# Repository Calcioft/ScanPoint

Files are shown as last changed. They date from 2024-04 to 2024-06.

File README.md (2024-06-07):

# ScanPoint

## Equipe

| Engenharia | Cargo | Membro | Matrícula |
| :- | :- | :- | :--: |
| Software | **Coordenadora geral** | Carla Rocha | 170085023 |
| Software | **Diretora de qualidade** | Brenda Santos | 180041444 |
| Software | **Diretor técnico de Software** | Denniel William | 170161871 |
| Aeroespacial | **Diretora técnica de Estrutura** | Maria Claudia | 200041193 |
| Energia | **Diretora técnica de Eletrônica/Energia** | Carolina Oliveira | 190011483 | 
| Aeroespacial | Desenvolvedor | Cássio Filho | 190011521 |
| Automotiva | Desenvolvedor | Diogo Soares | 190012188 |
| Eletrônica | Desenvolvedor | Miguel Munoz | 221008795 |
| Energia | Desenvolvedor | Lucas Pantoja | 190060352 |
| Software | Desenvolvedora | Ana Carolina | 190101792 |
| Software | Desenvolvedor | Guilherme Basilio | 160007615 |
| Software | Desenvolvedor | Artur de Souza | 190010606 |
| Software | Desenvolvedor | Ciro Costa | 190011611 |
| Software | Desenvolvedor | Vinicius Vieira | 190118059 |
| Software | Desenvolvedor | Pedro Menezes | 190139323 |

## Site

https://lappis-unb.gitlab.io/fga-pi2/semestre-2024-1/grupo-08/scanpoint/

## Como rodar os documentos
[Como rodar os documentos](./how-to-docs.md)

## Reuniões

| Dia | Horário |
| :--: | :--: |
| Quarta-feira | 16:00 - 18:00 |
| Sexta-feira | 14:00 - 18:00 |

## Entregas

### C1

Engloba as fases 1, 2 e 3 do ciclo de vida do projeto, sendo elas: **Problematização**, **concepção e detalhamento da solução** e **projeto e construção de subsistemas da solução proposta**.

**Geral**
- [Arquitetura](docs/geral/anexo.md)
- [Cronograma](docs/geral/cronograma.md)
- [EAP](docs/geral/eap_geral.md)
- [Estimativa de Custos](docs/geral/estimativa-custos.md)
- [Levantamento de riscos](docs/geral/FMEA.md)
- [Requisitos Gerais](docs/geral/requisitos.md)
- [Termo de Abertura](docs/geral/termo_de_abertura_de_projeto.md)
- [Visao geral](docs/geral/visaogeral.md)
- [Integracao de Áreas](docs/geral/integracao.md)

**Software**
- [Arquitetura de software](docs/software/arquitetura.md)
- [Backlog do produto](docs/software/backlog_produto.md)
- [Casos de uso](docs/software/casos-de-uso.md)
- [Diagrama BPMN](docs/software/diagrama-bpmn.md)
- [Diagrama de pacotes](docs/software/diagrama-de-pacotes.md)
- [EAP](docs/software/eap_software.md)
- [Funcionalidades](docs/software/funcionalidades.md)
- [Documento de identidade](docs/software/identidade.md)
- [Prototipo de alta Fidelidade](docs/software/prototipo.md)
- [Requisitos de software](docs/software/requisitos.md)
- [Projeto de subsistema de Software](docs/software/subsistema-software.md)

**Eletrônica/Energia**
- [Arquitetura de Eletrônica](docs/eletronica-energia/arquitetura_eletronica.md)
- [Arquitetura de Energia](docs/eletronica-energia/arquitetura_energia.md)
- [EAP](docs/eletronica-energia/eap.md)
- [Subsistema de Eletrônica](docs/eletronica-energia/Projeto_subsistema_eletronica.md)
- [Subsistema de Energia](docs/eletronica-energia/Projeto_Subsistema_Energia.md)
- [Requisitos](docs/eletronica-energia/requisitos-eletronica-energia.md)

**Estruturas**
- [EAP](docs/estruturas/EAP_estruturas.md)
- [Requisitos](docs/estruturas/Requisitos_estruturas.md)
- [Arquitetura](docs/estruturas/arquitetura_subs_estruturas.md)
- [Subsistema](docs/estruturas/Projeto_subsistema_estruturas.md)
- [Desenhos técnicos](docs/estruturas/DTs.md)
- [Manual de montagem](docs/estruturas/Manual_montagem_estruturas.md)

### C2

Diz respeito à primeira parte da fase 4, a **integração de subsistemas**. Serão feitas:

- Apresentação das adequações realizadas no projeto;
- Demonstração de funcionamento de todos os subsistemas que compõe a solução, já considerando a integração entre as respectivas partes

### C3

Diz respeito à segunda parte da fase 4, a **finalização do produto**. Serão entregues:

- Testes de integração e funcionamento do protótipo de produto;

- Demonstração do funcionamento completo da solução;

- Documentação técnica atualizada nos repositórios do projeto;

- Bannner de apresentação do projeto;

- Vídeo de propaganda da solução, contemplando seu funcionamento completo.

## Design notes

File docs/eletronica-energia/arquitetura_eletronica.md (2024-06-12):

# Arquitetura do Subsistema de Eletrônica

<p style="text-align:justify;">
O principal objetivo da execução do projeto do subsistema eletrônico é de garantir o controle preciso e eficiente do sistema, permitindo o funcionamento adequado do scanner e da mesa rotatória. Para isso, é necessário selecionar e integrar os componentes eletrônicos de forma a atender aos requisitos funcionais e não funcionais estabelecidos.
</p>

<p style="text-align:justify;">
A arquitetura do subsistema envolve motores de passo, microcontroladores Arduino Uno, a ponte H (L298N) e um regulador de tensão LM2596. Os motores de passo controlam a rotação da mesa e a altura da câmera, enquanto os microcontroladores Arduino Uno manipulam os dados de escaneamento e controlam os motores. A ponte H facilita a comunicação entre os motores e os Arduinos, permitindo o controle bidirecional necessário.
</p>

<p style="text-align:justify;">
A alimentação do sistema é fornecida por uma bateria de 12V, com o regulador de tensão LM2596 ajustando a tensão para 5V, conforme necessário para os componentes eletrônicos. Essa configuração assegura que todos os elementos do sistema recebam a energia adequada para um funcionamento estável e eficiente.
</p>

<p style="text-align:justify;">
Ao longo do desenvolvimento, serão realizadas simulações dos circuitos utilizando softwares como Proteus e Fritzing. Essas simulações, juntamente com diagramas de blocos do circuito e diagramas de barramento, proporcionarão uma visão abrangente e detalhada da arquitetura do subsistema eletrônico, facilitando a compreensão e verificação do projeto. 
</p>

## Versionamento

| Versão | Data | Modificação | Autor |
| --- | --- | --- | --- |
| 0.1 | 03/05/2024 | Criação do documento | Carolina Oliveira, Miguel Munoz |
| 0.2 | 03/05/2024 | Adição de versionamento | Ciro Costa  |
| 0.3 | 04/05/2024 | Ajustes de formatação | Ana Carolina |
| 0.4 | 04/05/2024 | Atualização da formatação | Carolina |
| 1.0 | 07/06/2024 | Adequação da Arquitetura conforme feedback do PC 1 | Carolina |

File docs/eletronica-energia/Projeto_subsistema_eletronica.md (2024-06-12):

# Projeto do Subsistema de Eletrônica

<p style="text-align:justify;">
O subsistema eletrônico desempenha o papel de controle sobre os motores, comunicação com o software, integração dos sensores. Nesse contexto, o foco da equipe consistiu na seleção dos componentes eletrônicos e na implementação de estratégias de gerenciamento em conformidade estrita com as normas de segurança elétrica pertinentes.
</p>

## 1. Motor de Passo

<p style="text-align:justify;">
O Motor de Passo é um motor elétrico utilizado para controle de movimentos de forma precisa, este controle é feito através de passos ou graus, com isso é possível controlar o motor sem o uso de sensores para determinar posição. Os motores desse tipo são controlados através de sinais digitais enviados para as suas bobinas, possibilitando a rotação fracionada do eixo, sem a necessidade de escovas internas <a href="#ref-1"> [1]</a>.
</p>

### 1.1. Estrutura do Motor de Passo
<p style="text-align:justify;">
As características do Motor de Passo, no que diz respeito à velocidade, torque e resolução são definidas primeiramente pela estrutura do motor, então é importante conhecer os aspectos internos e a função das peças que compõem o motor.
</p>

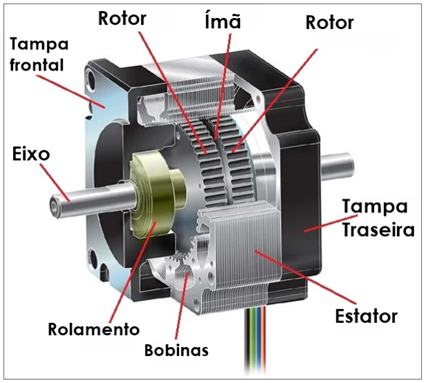
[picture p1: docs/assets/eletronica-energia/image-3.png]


<font size="2"><p style="text-align: center">Figura 1: Estrutura interna do motor de passo <a href="#ref-1"> [1]. </a></p></font>

#### 1.1.1. Rotor
<p style="text-align:justify;">
Uma das partes mais importantes do motor de passo é o rotor, na Figura 1, é mostrado  um motor com rotor híbrido, o corpo que representa o rotor híbrido é composto pelos dois rotores e o imã entre eles, utilizado para a polarização do rotor frontal e o traseiro <a href="#ref-1"> [1]</a>.
</p>

<p style="text-align:justify;">
Existem três configurações possíveis de montagem para o rotor: rotor de imã permanente, rotor de relutância variável e rotor híbrido, o tipo híbrido é o mais comumente utilizado, estas diferenças são apresentadas na Tabela 1.
</p>

<font size="2"><p style="text-align: center">Tabela 1: Diferenças entre os rotores.</p></font>

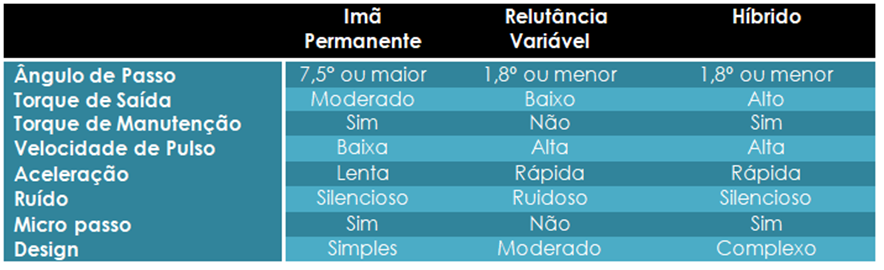
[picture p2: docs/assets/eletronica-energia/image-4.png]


#### 1.1.2. Estator
<p style="text-align:justify;">
O Estator produz o campo magnético que causa a movimentação do rotor. Para análise do estator é necessário tomar nota de alguns pontos como: o número de fases, de par de polos e configuração do fio. A fase ou o par de polos é formado por duplas de bobinas que são energizadas simultaneamente.
</p>

<p style="text-align:justify;">
A estrutura do estator é formada por polos magnéticos dentados, sendo que cada polo é dotado de uma bobina com o seu par oposto, de forma que os pares são energizados simultaneamente e por consequência são magnetizados com a mesma polaridade, os dois polos formam uma fase. 
</p>

<p style="text-align:justify;">
O primeiro modelo do exemplo abaixo é do tipo estator bifásico, com fases A e B, enquanto o segundo é do tipo estator trifásico, com fases A, B e C.
</p>

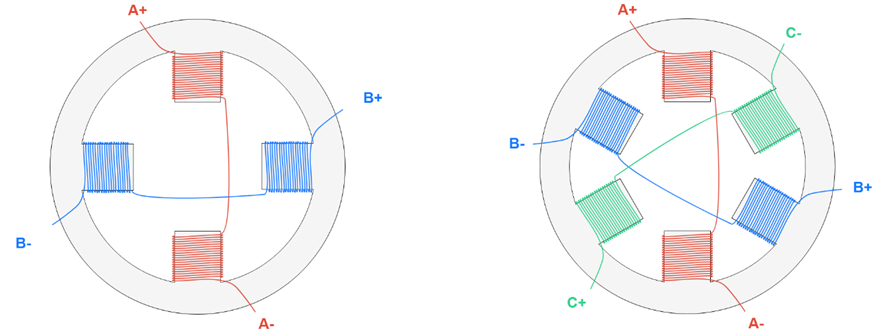
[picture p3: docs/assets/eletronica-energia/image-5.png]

<font size="2"><p style="text-align: center">Figura 2: Modelo de um estator bifásico.</p></font>

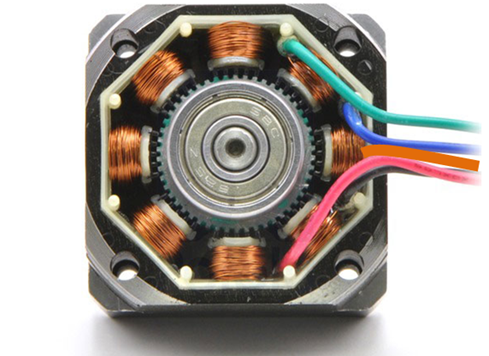
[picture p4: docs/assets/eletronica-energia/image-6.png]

<font size="2"><p style="text-align: center">Figura 3: Estator real.</p></font>

<p style="text-align:justify;">
A Figura 2, mostra uma representação gráfica da distribuição das bobinas no estator, já a Figura 3, mostra uma imagem de um estator real, com seus dentes e bobinas em enrolamento de cobre.
</p>

<p style="text-align:justify;">
O eixo do motor híbrido é construído com dois grupos dentados de rotores, um deles polarizados com polo sul e outro com polo norte.
</p>

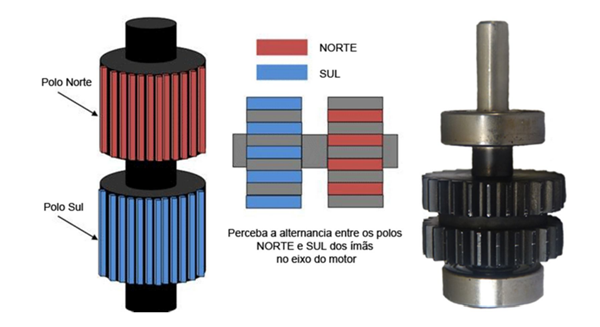
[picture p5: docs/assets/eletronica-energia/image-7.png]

<font size="2"><p style="text-align: center">Figura 4: Modelo do eixo do motor <a href="#ref-1"> [1]</a>.</p></font>

### 1.2. Tipos de Polos
<p style="text-align:justify;">
Existem dois modelos de acordo com os polos, o bipolar e o unipolar, os termos surgiram de conformidade com os drivers que são utilizados para acionamento desses motores. O polar do termo representa "polaridade” e se refere ao driver utilizado para controle desses motores, utilizaremos as expressões "motor unipolar” e "motor bipolar” por convenção social <a href="#ref-1"> [1]</a>.
</p>
 
#### 1.2.1. Unipolar
<p style="text-align:justify;">
O modelo utilizado com o driver Unipolar conta com duas bobinas por fase, formando um par de polos, além disso, há o contato em comum, dessa forma os motores desse tipo podem ter 5, 6 ou 8 fios <a href="#ref-1"> [1]</a>.
</p>

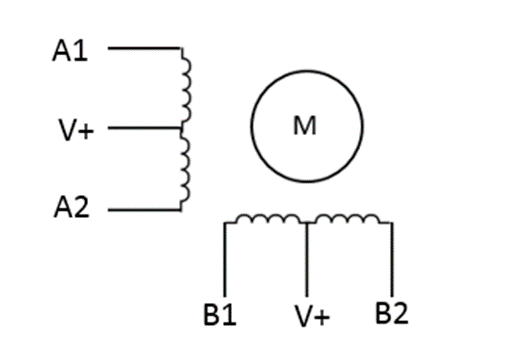
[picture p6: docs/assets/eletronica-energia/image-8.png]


<font size="2"><p style="text-align: center">Figura 5: Driver unipolar <a href="#ref-1"> [1]</a>.</p></font>

<p style="text-align:justify;">
Com o fio central é possível controlar a direção da corrente, no entanto apenas metade da bobina pode ser utilizada, isso faz com que o motor seja menos eficiente se comparado ao bipolar. O fio central é conectado ao Vin do circuito, sendo que se o Mosfet 1 estiver ativo, a corrente fluirá de Am para A+, se o Mosfet ativo for o 2, a corrente fluirá de Am para A-.
</p>

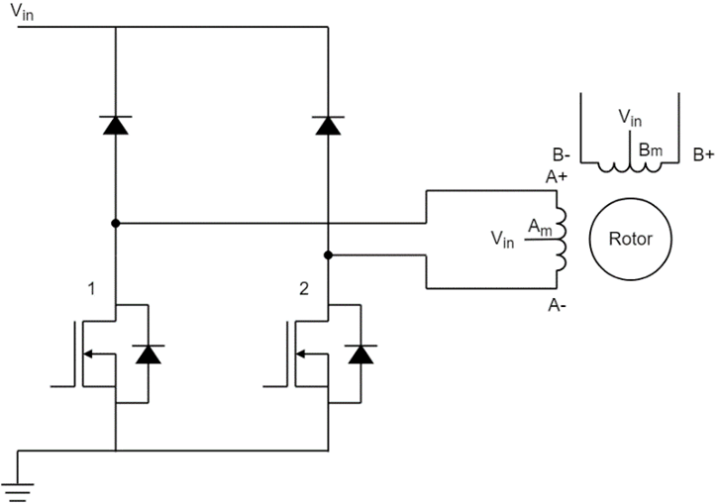
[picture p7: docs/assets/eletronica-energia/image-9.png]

<font size="2"><p style="text-align: center">Figura 6: Diagrama circuito unipolar <a href="#ref-1"> [1] </a>.</p></font>

#### 1.2.2. Bipolar
<p style="text-align:justify;">
No motor do tipo bipolar, cada bobina é composta por dois fios apenas, sem derivações centrais como as do tipo unipolar, de forma que são motores mais fáceis de serem produzidos.
</p>

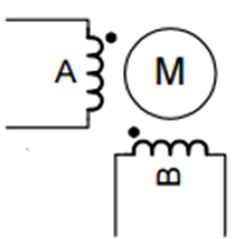
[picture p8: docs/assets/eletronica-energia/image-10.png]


<font size="2"><p style="text-align: center">Figura 7: Driver bipolar <a href="#ref-1"> [1]</a>.</p></font>

<p style="text-align:justify;">
Como não há a derivação central, para controle de direção é necessário utilizar uma ponte H, exigindo um circuito de acionamento mais complexo. Para os motores desse tipo, temos que a corrente flui de A- para A+ quando os Mofets 2 e 3 estão ativos, e flui de A+ para A- quando 1 e 4 estão ativos. Apesar de possuir um acionamento mais complexo, os motores do tipo bipolar são mais comuns, pois permitem que o motor atinja maior torque <a href="#ref-1"> [1]</a>. Importante mencionar que, para o desenvolvimento deste projeto, os motores bipolares foram adotados pois, além da disponibilidade desses componentes no laboratório da UnB, eles exigem a manipulação de menos fios, economizando conexões nas placas de controle que serão compartilhadas.
</p>

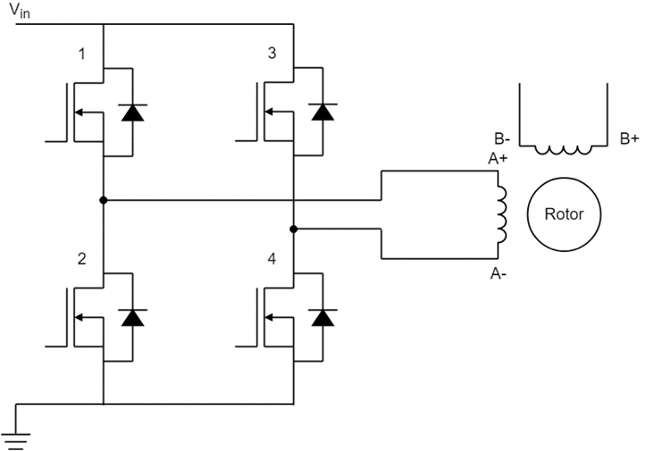
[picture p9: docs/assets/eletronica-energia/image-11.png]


<font size="2"><p style="text-align: center">Figura 8: Diagrama circuito bipolar <a href="#ref-1"> [1]</a>.</p></font>

### 1.3. Funcionamento de um motor de passo
<p style="text-align:justify;">
O motor de passo é um dispositivo eletromecânico composto por bobinas (indutores) e um rotor magnético (ímã permanente ou imantado). As bobinas convertem energia elétrica em campo magnético, alinhando o rotor a esse campo. A excitação correta das bobinas faz o rotor, que gira em torno de seu eixo, mover-se no sentido desejado, convertendo energia magnética em movimento (energia mecânica). O rotor é rotacionado em pequenos incrementos angulares, chamados de "passos" <a href="#ref-2"> [2]</a>.

O funcionamento básico do motor de passo envolve o uso de bobinas alinhadas dois a dois. Quando energizadas, elas atraem o rotor, alinhando-o com o campo magnético gerado, resultando em uma variação angular pequena, chamada de passo. A velocidade e o sentido de movimento são determinados pela forma como cada bobina é ativada, incluindo a ordem e a velocidade entre cada processo de ativação <a href="#ref-2"> [2]</a>.

As vantagens do motor de passo incluem sua precisão de posicionamento e torque aplicado, além de ter uma resposta excelente na aceleração e desaceleração, devido à sua lógica digital. No entanto, ele pode apresentar baixo desempenho em alta velocidade, requer um certo grau de complexidade para operação e pode sofrer ressonância devido a um controle inadequado <a href="#ref-2"> [2]</a>.

Complementando com o banco de dados, o motor de passo é frequentemente utilizado em aplicações que exigem precisão de posicionamento, como impressoras 3D, máquinas CNC e robótica industrial. Ele oferece um controle preciso sobre o movimento, o que é essencial em muitas aplicações. Além disso, o motor de passo pode ser facilmente controlado por microcontroladores, o que o torna uma escolha popular em projetos eletrônicos e de automação <a href="#ref-2"> [2]</a>.

A figura a seguir mostra como um motor de passo pode ser controlado mediante lógica binária:
</p>
 
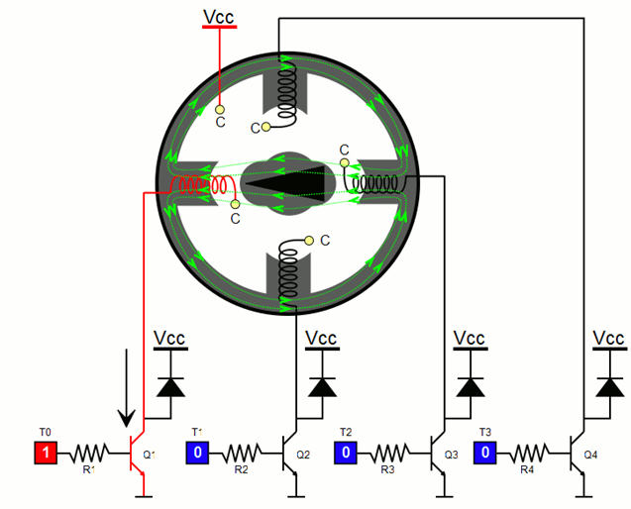
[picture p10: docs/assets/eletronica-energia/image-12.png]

<font size="2"><p style="text-align: center">Figura 9: Motor de passo controlado pelas entradas To até T3 <a href="#ref-2"> [2]</a>.</p></font>

## 2. Placa Arduino Uno
<p style="text-align:justify;">
O Arduino Uno é uma placa microcontrolada baseada no chip ATmega328. Esta placa é muito utilizada no desenvolvimento de projetos embarcados, é hoje em dia é a mais utilizada e documentada da família Arduino.
</p>

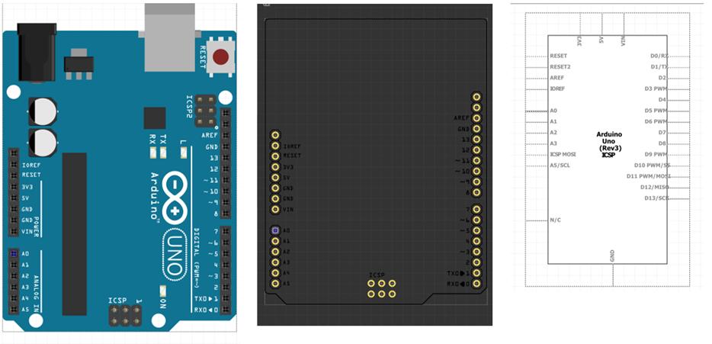
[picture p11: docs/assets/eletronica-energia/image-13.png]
   

<font size="2"><p style="text-align: center">Figura 10: Placa Arduino Uno, diagrama de barramento e diagrama esquemático. Fonte: Autoria própria.</p></font>

<p style="text-align:justify;">
A placa conta com um chip ATmega328 que é um microcontrolador único desenvolvido pela Atmel, pertencente à família megaAVR. A arquitetura do Arduino Uno segue o padrão Harvard e possui um núcleo de processador RISC de 8 bits customizado.
</p>

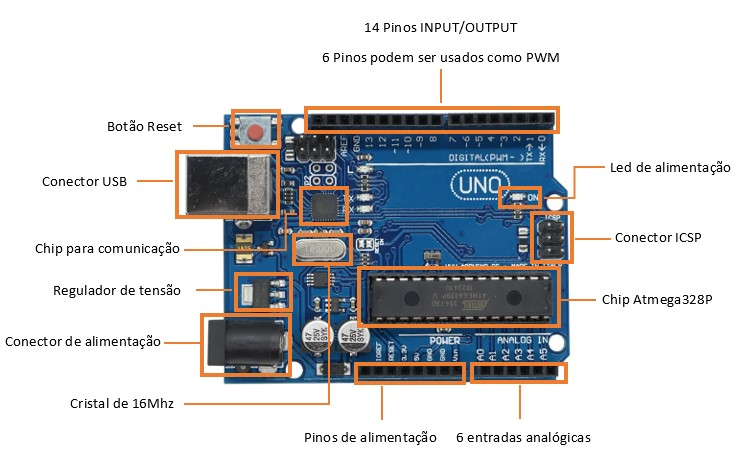
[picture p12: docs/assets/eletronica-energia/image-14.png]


<font size="2"><p style="text-align: center">Figura 11: Diagrama de pinos da placa Arduino Uno <a href="#ref-3"> [3]</a>.</p></font>

### 2.1. Características principais do Arduino Uno

 - A tensão de operação é 5V
 - A tensão de entrada recomendada varia de 7V a 12V
 - A tensão de entrada varia de 6V a 20V
 - 14 pinos de entrada/saída digital
 - 6 pinos analógicos
 - A corrente DC para cada pino de entrada/saída é de 40 mA
 - A corrente DC para o pino de 3,3 V é 50 mA
 - A memória flash é de 32 KB
 - SRAM é 2KB
 - EEPROM é 1 KB
 - A velocidade do CLK é de 16 MHz

### 2.2. Diagrama de pinos do Arduino Uno
<p style="text-align:justify;">
A placa do Arduino Uno conta com uma grande variedade de pinos de alimentação, pinos analógicos, ATmega328, conector ICSP, botão Reset, LED de alimentação, pinos digitais, led de teste, pinos TX/RX, interface USB e fonte de alimentação externa, na Figura 12, se apresentam estes pinos.
</p>

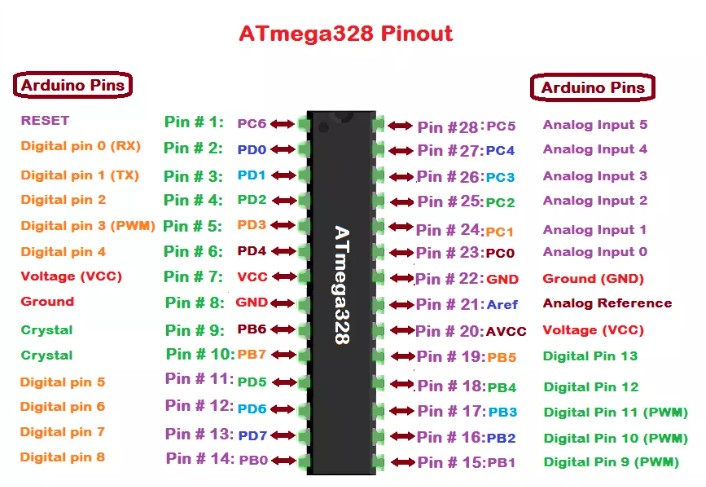
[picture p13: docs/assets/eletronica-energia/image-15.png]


<font size="2"><p style="text-align: center">Figura 12: Diagrama de Pinos do microcontrolador ATmega328.</p></font>

<p style="text-align:justify;">
A seguir se faz a descrição de cada um dos componentes do diagrama na Figura 12.
</p>

#### 2.2.1. Descrições principais para utilização do Arduino Uno

##### 2.2.1.1. Fonte de Alimentação
<p style="text-align:justify;">
Esta placa conta com uma grande vantagem e é poder ligar ela de forma externa com ajuda de um cabo USB ou uma fonte de alimentação externa, além disso, as fontes de alimentação externas incluem principalmente um conversor AC para DC, caso contrário, uma bateria. A fonte deve ser inserida no conector de alimentação da placa Arduino. Suas faxas de tensão estão entre 7 e 12 Volts,  conta com um pino GND e conector POWER <a href="#ref-3"> [3]</a>.
</p>

##### 2.2.1.2. Entradas e saídas digitais
<p style="text-align:justify;">
O Arduino Uno possui 14 pinos que podem ser usados como entrada ou saída a depender da necessidade do programador. Com a ajuda de funções como pinMode(), digitalWrite() e Digital Read() é possível definir como os pinos serão utilizados <a href="#ref-3"> [3]</a>.
</p>

##### 2.2.1.3. Entradas analógicas
<p style="text-align:justify;">
A placa Arduino UNO conta com 6 canais de conversor analógico para digital, nomeadas de A0 a A5. Sendo que a resolução do conversor analógico digital é de 10Bits. Isso significa que este irá mapear tensões entre 0 e a tensão operacional (5V ou 3.3V) para valores inteiros entre 0 e 1023. No Arduino UNO, isso permite uma resolução entre leituras de: 5 volts / 1024 unidades, ou .0049 volts (4.9 mV) por unidade. Essas entradas são nomeadas de A0 a A5. A função analogRead() lê o valor de um pino analógico especificado <a href="#ref-3"> [3]</a>.
</p>

#### 2.2.2. Pino (TX) e Pino (RX) (Serial):

<p style="text-align:justify;">
  Os pinos 0 e 1 são usados para transmitir e receber dados seriais TTL, e estes são conectados aos pinos equivalentes do chip ATmega8U2 USB para TTL Serial <a href="#ref-3"> [3]</a>.
</p>

#### 2.2.3. Pinos externos de interrupção:
<p style="text-align:justify;">
Os pinos 2 e 3 do Arduino Uno podem desempenhar a função de entrada de sinal para interrupção externa tais funções são nomeadas de INT0 e INT1, respectivamente <a href="#ref-3"> [3]</a>.
</p>

#### 2.2.4. Pinos 3, 5, 6, 9, 10 e 11 (PWM):
<p style="text-align:justify;">
O Arduino Uno possui 6 pinos para saída PWM, são estes os pinos 3, 5, 6, 9, 10 e 11. Para auxiliar na manipulação desses pinos a plataforma possui uma função que auxilia na escrita de valores chamada de "duty cycle” facilitando a utilização do PWM do Arduino Uno, o qual pode ser acoplado com módulos externos <a href="#ref-3"> [3]</a>.
</p>

#### 2.2.5. Pinos SPI (Pino-10 (SS), Pino-11 (MOSI), Pino-12 (MISO), Pino-13 (SCK):
<p style="text-align:justify;">
SPI (Serial Peripheral Interface) é um protocolo de comunicação serial, a SPI possui uma conexão full duplex, o que significa que os dados são enviados e recebidos simultaneamente. O SPI pode ser utilizado para a comunicação entre dois arduinos <a href="#ref-3"> [3]</a>.
</p>

#### 2.2.6. LED Interno Pino 13
<p style="text-align:justify;">
A placa do Arduino Uno possui um Led interno conectado ao pino 13 (pino digital). Como pino de valor ALTO, o diodo emissor de luz é ativado, sempre que o pino estiver em nível BAIXO <a href="#ref-3"> [3]</a>.
</p>

#### 2.2.7. Pino-4 (SDA) e Pino-5 (SCL) (I2C):
<p style="text-align:justify;">
Permite comunicação TWI (Two Wire Interface) com a ajuda da biblioteca Wire <a href="#ref-3"> [3]</a>.
</p>

#### 2.2.8. AREF (Tensão de Referência):
<p style="text-align:justify;">
AREF significa Referência Analógica. Ele permite alimentar o Arduino com uma tensão de referência de uma fonte de alimentação externa para configurar a tensão de referência usada para entrada analógica (ou seja, o valor usado como o topo da faixa de entrada) <a href="#ref-3"> [3]</a>.
</p>

#### 2.2.9. Pino de Reset:
<p style="text-align:justify;">
Este pino é usado para resetar (RST) o microcontrolador <a href="#ref-3"> [3]</a>.
</p>
 
### 2.3. Memória
<p style="text-align:justify;">
A memória do microcontrolador Atmega328 do Arduino Uno inclui memória flash de 32 KB para armazenamento de código, SRAM-2 KB e EEPROM-1 KB <a href="#ref-3"> [3]</a>.
</p>

### 2.4. Comunicação
<p style="text-align:justify;">
O Arduino Uno ATmega328 oferece comunicação serial UART TTL e é acessível em pinos digitais como TX (1) e RX (0). O software de um Arduino possui um monitor serial que permite dados fáceis. Existem dois LEDs na placa, como RX e TX, que piscarão sempre que os dados estiverem sendo transmitidos através do USB.
</p>

<p style="text-align:justify;">
A biblioteca SoftwareSerial permite a comunicação serial nos pinos digitais do Arduino Uno e o ATmega328P suporta TWI (I2C), bem como comunicação SPI. O software Arduino contém uma biblioteca cabeada para simplificar a utilização do barramento I2C <a href="#ref-3"> [3]</a>.
</p>

### 2.5. Proteção de alta tensão do USB
<p style="text-align:justify;">
A placa Arduino Uno possui um fusível que protege a porta USB do PC de sobretensão. Embora a maioria dos PCs tenha sua própria proteção interna, o fusível oferece uma proteção adicional de segurança <a href="#ref-3"> [3]</a>.
</p>

### 2.6. Características físicas
<p style="text-align:justify;">
As características físicas de uma placa Arduino incluem principalmente comprimento e largura. O comprimento e a largura da placa de circuito impresso do Arduino Uno são 2,7 X 2,1 polegadas, mas o conector de alimentação e o conector USB se estenderão além dessa medida. A placa pode ser fixada na superfície, caso contrário, com os orifícios dos parafusos <a href="#ref-3"> [3]</a>.
</p>

## 3. Modulação PWM
<p style="text-align:justify;">
A modulação por largura de pulso (PWM) é uma técnica fundamental que envolve a variação da largura dos pulsos em um sinal elétrico para transmitir informações. Em vez de manter um sinal em níveis constantes, o PWM altera a largura dos pulsos, controlando o tempo em que a chave fica ligada e desligada. Isso permite administrar a quantidade média de energia que chega à carga e, consequentemente, a potência elétrica <a href="#ref-4"> [4]</a>.

Essa técnica é amplamente utilizada em diversos equipamentos eletrônicos de potência, como drivers de LED, inversores de frequência e controle de velocidade de motores. No cotidiano, o PWM é encontrado em carregadores, sistemas fotovoltaicos, servo-motores e carros elétricos, entre outros <a href="#ref-7"> [7]</a>.

O ciclo de trabalho, ou Duty Cycle mostrado na figura, é um parâmetro crucial para controlar um sinal PWM. Ele representa a relação entre a largura do pulso e o período, informando o tempo em que o sinal está em nível alto (ligado) e o tempo em que está em nível baixo (desligado). 

O Duty Cycle é expresso em porcentagem e calculado pela fórmula D = (PW / T) x 100%, onde PW é a largura do pulso e T é o período <a href="#ref-5"> [5]</a>. Deste modo, o sinal 255 da placa é convertido para um sinal PWM de 100%, e o sinal 0 da placa é convertido para um sinal PWM de 0%. Portanto um sinal de 127 da placa será convertido para um sinal PWM de 50%. Consequentemente, para um motor, o sinal 0 seria o motor parado, já o sinal 255 seria a sua rotação máxima. Abaixo é possível ver um exemplo com o sinal PWM sendo aplicado em um LED <a href="#ref-5"> [5]</a>.
</p>

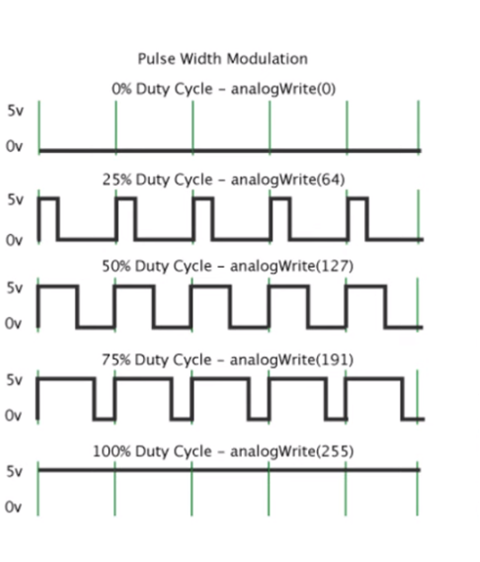
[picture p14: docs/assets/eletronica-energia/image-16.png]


<font size="2"><p style="text-align: center">Figura 13: Representação do comportamento do controle PWM.</p></font>

<p style="text-align:justify;">
Uma das principais vantagens do PWM é a manutenção do sinal digital em todo o percurso, o que minimiza os efeitos de ruído. Além disso, o PWM oferece maior imunidade ao ruído em comparação ao controle analógico, o que torna essa técnica ideal para comunicações. Em sistemas de freios controlados por modulação, por exemplo, o PWM é utilizado para controlar a pressão exercida pelo freio de acordo com a quantidade de tensão ou corrente aplicada <a href="#ref-4"> [4]</a>.
</p>

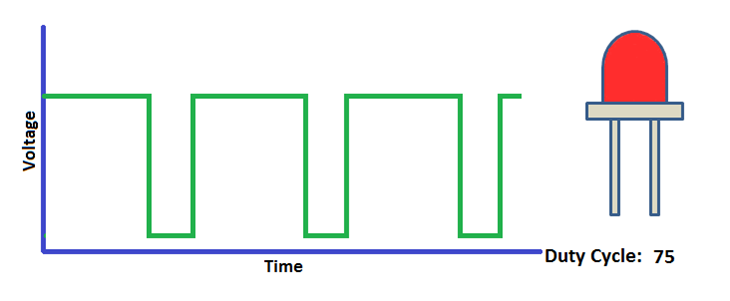
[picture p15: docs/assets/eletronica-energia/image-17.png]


<font size="2"><p style="text-align: center">Figura 14: Funcionamento do PWM num led.
Fonte <a href="#ref-5"> [5]</a>.</p></font>

## 4. Driver Motor de Passo A4988

<p style="text-align:justify;"> O Driver A4988 é um componente eletrônico utilizado para controlar motores de passo bipolares, com capacidade de pequenos passos (microstepping) para maior suavidade e precisão na movimentação dos motores.  A tensão de operação lógica do driver é de 3-5,5V, que são conectados nos pinos VDD e GND. Pode controlar motores de até 35V e 2A por bobina (picos de 4A), além disso, é capaz de controlar o motor com até 1/16 passos <a href="#ref-4"> [9]</a>
</p>

### 4.1. Calibração

<p style="text-align:justify;">
Para calibrar o driver de motor faz-se o ajuste do trimpot integrado à placa. Para realizar a calibração deve-se utilizar a seguinte fórmula para cálculo da tensão de referência:
</p>

Vref = Imotor x 8 x Rsense

<p style="text-align:justify;">
Onde Vref é a tensão de referência que devemos chegar no ajuste do driver, 8 é uma constante arbitrária específica para o A4988, e Rsense é o resistor de detecção de corrente presente no driver e Imotor é a corrente de trabalho no motor.  A corrente máxima de um motor está indicada no seu datasheet, e em geral recomenda-se utilizar até 70% desse valor <a href="#ref-4"> [9]</a>.
</p>

### 4.2. Ajuste do A4988

<p style="text-align:justify;">
Com o valor da tensão de referência determinado, precisamos fazer o ajuste do potenciômetro. Não é preciso que o driver esteja conectado na placa da aplicação final, basta ligar os pinos RST e SLP do driver e alimentar parte lógica através dos pinos Vdd e GND do módulo. Com essas ligações, é medido com um multímetro a tensão entre o GND e a parte metálica do trimpot, onde é feito o ajuste. Girar o potenciômetro no sentido horário aumenta a tensão e no sentido anti-horário diminui. O ajuste deve ser feito até a leitura do multímetro coincidir com a tensão calculada <a href="#ref-4"> [9]</a>. </p>

### 4.3. Uso do driver A4988
<p style="text-align:justify;">
Para usar o driver é simples, conecte a alimentação do motor aos pinos Vmot e GND e a alimentação da parte lógica aos pintos Vdd e GND. O pino DIR controla a direção em que o motor deve girar e o pino STEP faz o motor dar um passo a cada pulso que recebe <a href="#ref-4"> [9]</a>.</p>

### 4.4. Especificações técnicas do Driver Motor de Passo A4988
– Chip: A4988 (datasheet)
– Controle de passos e direção.
– Tensão lógica: 3-5,5V
– Tensão saída motores: 8-35V
– 5 Resoluções: full-step, half-step, 1/4-step, 1/8-step e 1/16-step.
– Regulador de tensão embutido.
– Proteção conta sobrecarga de corrente e curto-circuito.
 
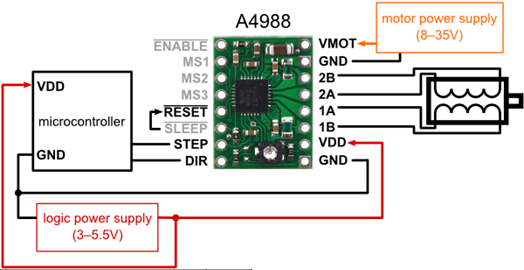
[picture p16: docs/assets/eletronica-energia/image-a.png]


<font size="2"><p style="text-align: center">Figura 15: Diagrama esquemático do drive A4988.
Fonte <a href="#ref-5"> [9]</a>.</p></font>

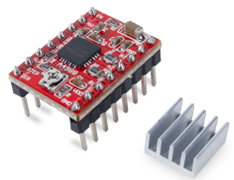
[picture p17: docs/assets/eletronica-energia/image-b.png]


<font size="2"><p style="text-align: center">Figura 16: Drive do motor de passo.
Fonte <a href="#ref-5"> [5]</a>.</p></font>

Tabela: Conexões do driver A4988 <a href="#ref-5"> [6]</a>.</p>

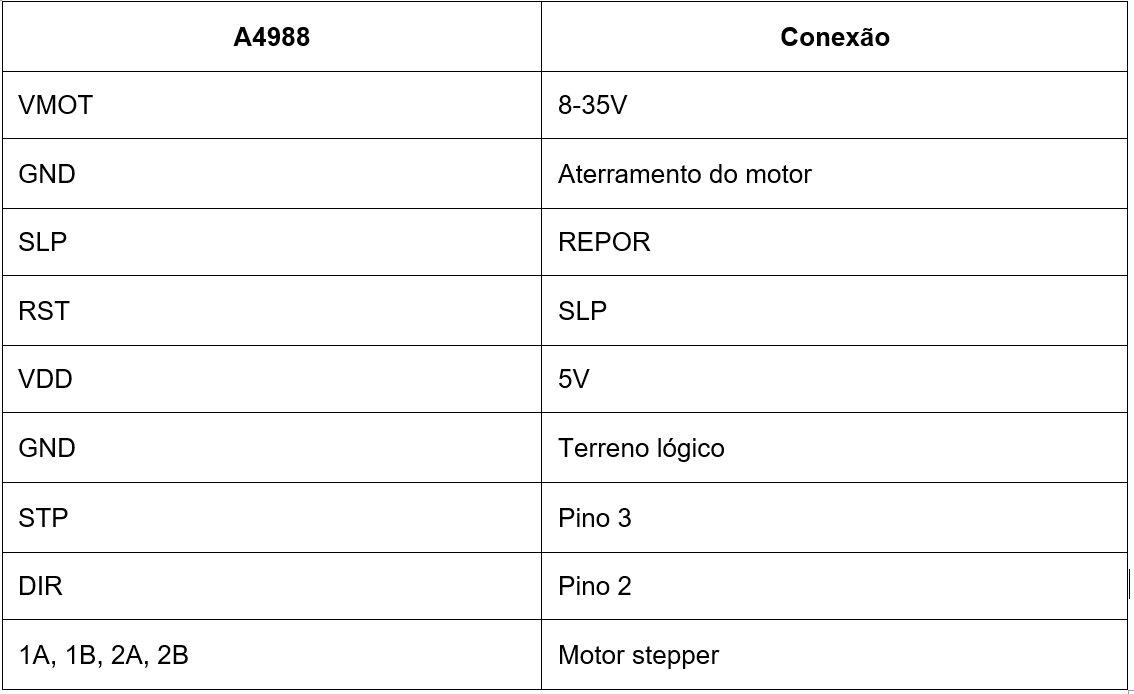
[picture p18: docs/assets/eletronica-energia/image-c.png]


### 4.5. Sensores de Distância Laser VL53L0X
<p style="text-align:justify;">
O VL53L0X é um sensor de distância infravermelho de alta precisão, produzido pela STMicroelectronics, conhecido como o menor sensor do mercado. Utiliza um VCSEL (Laser Emissor de Superfície de Cavidade Vertical) com filtros para evitar interferências de luz externa, aumentando seu alcance. Funciona como um sensor Time of Flight (ToF), emitindo uma luz invisível que reflete em obstáculos, e calcula a distância com base no tempo de retorno dessa luz, alcançando até 2 metros <a href="#ref-4"> [10]</a>.

O módulo VL53L0X, também conhecido como GY-VL53L0XV2, CJVL53L0XV2 ou VL53L0XV2, é compatível com várias placas Arduino. É compacto, preciso, possui regulador de tensão integrado, permitindo alimentação de 3V ou 5V, e vem em várias cores, todas com as mesmas funcionalidades. A comunicação é realizada via interface I2C  <a href="#ref-4"> [10]</a>. </p>

### 4.6. Pinagem
<p style="text-align:justify;">
Além de pinos de alimentação (VIN e GND), o módulo VL53L0X possui dois pinos dedicados a comunicação I2C (SCL e SDA), um pino de reset (XSHUT) e um pino de saída de dados (GPIO1) que pode ser utilizado para programar interrupções no microcontrolador ao qual o sensor está ligado  <a href="#ref-4"> [11]</a>.
</p>

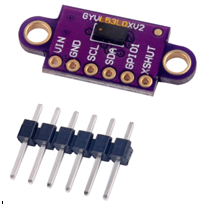
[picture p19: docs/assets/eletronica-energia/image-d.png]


<font size="2"><p style="text-align: center">Figura 17: Módulo VL53L0X.
Fonte <a href="#ref-5"> [11]</a>.</p></font>

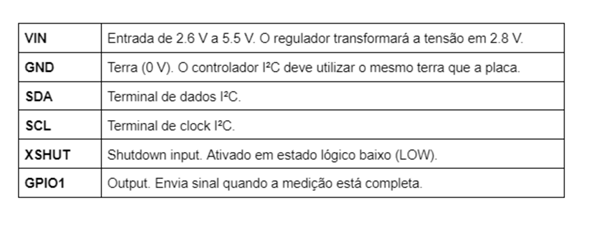
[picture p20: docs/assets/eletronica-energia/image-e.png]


<font size="2"><p style="text-align: center">Figura 18: descrição dos pinos do VL53L0X.
Fonte <a href="#ref-5"> [11]</a>.</p></font>

## 5. Módulo Regulador C/LM2596
<p style="text-align:justify;">
O circuito precisa de um módulo que permita trabalhar com duas tensões, uma de 12V para alimentar a Ponte H, e um de 5V para alimentar a placa de árduino, para resolver esta situação foi trabalhado com um fonte de 12V e um módulo regular C/LM2596 (ver figura 16 e 17). O Módulo Regulador de Tensão LM2596 trabalha como um conversor DC DC no modo Step Down, sendo capaz de reduzir uma carga de até 3A com ótima eficiência. 

A tensão de saída pode ser ajustada entre 1,5 a 35v, tendo como entrada 3,2 a 40v. Possui uma velocidade de comutação de 150KHz e pode ser aplicado em circuitos onde a saída de um sensor é superior a 5v, tensão de entrada máxima em um Arduino ou PIC <a href="#ref-8"> [8]</a>.
</p>

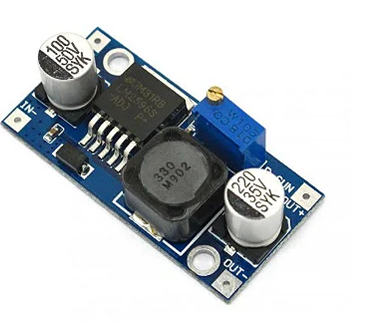
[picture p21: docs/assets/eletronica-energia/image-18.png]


<font size="2"><p style="text-align: center">Figura 19: Módulo regular C/LM2596.</p></font>

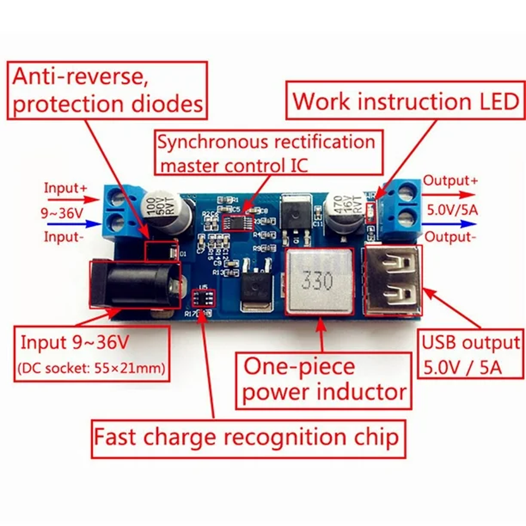
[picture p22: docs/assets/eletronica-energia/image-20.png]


<font size="2"><p style="text-align: center">Figura 20: Especificação dos componentes do módulo regulador C/LM2596.</p></font>

<p style="text-align:justify;">
Este módulo tem as seguintes carácterísticas:
</p>

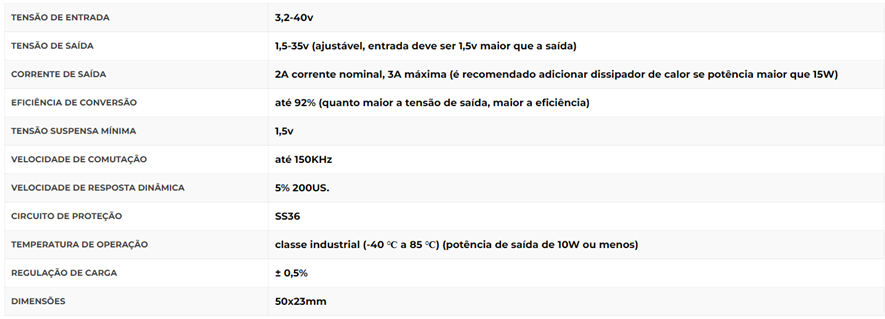
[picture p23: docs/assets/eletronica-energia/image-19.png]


<p style="text-align:justify;">
Assim conhecendo todos os componentes, foi montada uma simulação utilizando programa wokwi, a qual é motrada na Figura 21, esta simulação foi importante para verificar o funcinamento da programação antes de realizar testes reais. Já na Figura 22, encontra-se a representação do circuito realizada utilizando o Fritzing que permite gerar o diagrama esquemáticos e de barramento os quais são apresentados nas figuras 23 e 24 respectivamente </p>

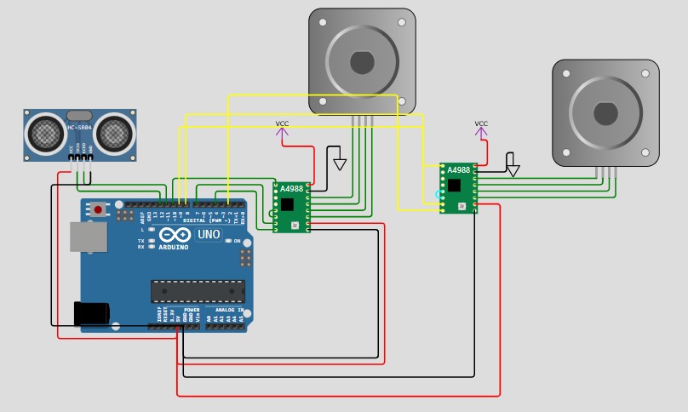
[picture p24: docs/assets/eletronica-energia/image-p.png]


<font size="2"><p style="text-align: center">Figura 21: Simulação do wokwi do sistema de motores.</p></font>



<font size="2"><p style="text-align: center">Figura 22: Sistema realizado no Fritzing para gerar os diagramas.</p></font>



<font size="2"><p style="text-align: center">Figura 23: Diagrama de blocos completo do circuito com motores de passo.</p></font>



<font size="2"><p style="text-align: center">Figura 24: Diagrama de barramentos completo do circuito com motores de passo.</p></font>

## 6. Descrição Matemática do Motor
<p style="text-align:justify;">
Um motor pode ser modelado utilizando um Resistor, um indutor e uma força contra eletromotriz que relaciona o fluxo magnético gerado pelo motor em função do fluxo magnético e do número de espiras que ele tem, sendo assim esta força é modelada pela relação de Faraday como se mostra na equação 1:
</p>



<p style="text-align:justify;">
A equação que representa a tensão pode ser modelada aplicando a LKT, representada como mostra a equação 2 e a Figura 25:
</p>





<font size="2"><p style="text-align: center">Figura 25: Modelo Elétrico do motor DC.</p></font>

<p style="text-align:justify;">
O motor pode ser separado em variáveis elétricas e mecânicas, conforme mostra a figura 26, onde a parte ressaltada na cor preto, indica a parte elétrica e a ressaltada na cor vermelho a parte mecânica como.
</p>



<font size="2"><p style="text-align: center">Figura 26: Modelo elétrico e mecânico do motor DC.</p></font>

Sendo:
- R: resistência interna do motor
- Va: tensão aplicada ao motor
- L: indutância interna do motor
- i: corrente elétrica consumida pelo motor
- e: força contra eletromotriz
- ω: velocidade angular do rotor
- τ: torque provado pelo rotor
- J: momento de inércia do rotor do motor

<p style="text-align:justify;">
O campo incidente sobre o motor é chamado campo fixo, esse campo fixo pode ser gerado por uma bobina ou imã permanente, supondo que a corrente elétrica de campo constante, descartando efeitos secundários, em uma máquina rotativa a variação do fluxo magnético sobre a bobina é proporcionar a velocidade angular como mostra a equação 3.
</p>



<font size="2"><p style="text-align: center">Figura 27: Representação do campo magnético no motor.</p></font>



<p style="text-align:justify;">
Assim a força contra eletromotriz é proporcional ao fluxo, desta forma pode ser representada como mostra a equação 4:
</p>



<p style="text-align:justify;">
Como a força exercida nos condutores é proporcional à corrente elétrica que passa pelo condutor, o torque do motor é proporcional à corrente, e se iguala quando se utiliza uma constante de torque \( Kt \), como mostra a equação 5.
</p>



<p style="text-align:justify;">
Assim a potência é produto do torque pela velocidade angular desenvolvida pelo motor, desta forma:
</p>



<p style="text-align:justify;">
Outro parâmetro considerado é o torque inercial, o qual tem como trabalho suprimir todas as perdas e ser suficiente para acelerar o motor até um ponto de inércia, ele pode ser representado como a equação 7:
</p>





<p style="text-align:justify;">
O torque total de atrito do motor ou de arrasto, depende da velocidade angular do motor, ele é dependente do coeficiente de arrasto ou atrito viscoso do motor, assim o torque total do motor é:
</p>



<p style="text-align:justify;">
Substituindo o torque total, encontra-se a relação de corrente como mostra a equação 9:
</p>



<p style="text-align:justify;">
Substituído a corrente na equação geral do motor, encontramos a representação da velocidade angular em função da velocidade de entrada do motor, como mostra equação 10:
</p>



<p style="text-align:justify;">
Realizando procedimentos matemáticos, e derivando o termo do indutor e reagrupando termos é obtida a equação diferencial não homogênea mostrada na equação 11:
</p>



<p style="text-align:justify;">
A velocidade máxima pode ser calculada como:
</p>



<p style="text-align:justify;">
Aplicando a transformada de Laplace para a EDO com condições iniciais nulas, encontra-se a função de transferência geral descrita na equação:
</p>



## 7. Cálculo dos Parâmetros do Motor
<p style="text-align:justify;">
Para calcular os parâmetros do motor, é necessário conhecer as características dele publicadas pelo fabricante, considerando que os motores de passo tem o código NEMA 17 4.2 Kgf 1.7 A (Stepper Motor 17HS4401).
</p>

### 7.1. Especificações do Motor de Passo

- Ângulo do passo: 1.8 °
- Tensão de Retenção: 3 V
- Tensão nominal: 4,8 V
- Resistência: ~1.8 Ohms
- Inércia do Rotor: 38g cm²
- Corrente de Retenção: 1.7 A
- Rosca frontal: M3
- Enrolamento: Espiras bifilares
- Temperatura máxima de operação: 80 °C
- Temperatura ambiente: -10 °C a 50 °C
- Classe de isolamento: B
- Torque: 4,2 Kgf.cm
- Indutância por Fase: 2,3 mH
- Quantidade de fios: 4
- Comprimento do cabo: 100 cm
- Comprimento do eixo exposto: 20 mm
- Diâmetro do eixo: 5 mm
- Dimensões do motor (C x L x A): 42 x 42 x 39 mm (ignorando o eixo)
- Peso do motor: 280 g

<p style="text-align:justify;">
Os cálculos feitos são apresentado na Tabela 2:
</p>

<font size="2"><p style="text-align: center">Tabela 2: Cálculos do motor de passo.</p></font>



<p style="text-align:justify;">
Substituindo na função de transferência mostrada na equação 12, é encontrada a representação do motor DC:
</p>



<p style="text-align:justify;">
A equação diferencial é representada como:
</p>



<p style="text-align:justify;">
Fazendo uma representação da função de transferência utilizando um degrau unitário, foi encontrado o comportamento mostrado na Figura 28.
</p>



<font size="2"><p style="text-align: center">Figura 28: Função de transferência do motor de Passo.</p></font>

<p style="text-align:justify;">
É observado que o comporamento matemático do motor passo tem um comportamento de primeira ordem, más, na equação 12, foi mostrado que este era de segunda ordem, o que indica que o efieto de segunda ordem é pouco relevante para este sistema, por esse motivo foi feita uma aproximação para um modelo de primeira ordem, assim, foi feito um procedimento matemático para encontrar essa aproximação considerando que o termo de segunda ordem está em relação ao indutor, e sua contribuição é pequena, este parâmetro foi aproximado a zero, assim a EDO da equação 11 fica como mostra a equação 13.
</p>





<p style="text-align:justify;">
Fazendo a representação da equação de transferência proposta na equação 15 e comparando com a função de transferência mostrada na equação 14, é verificado, que efetivamente o sistema pode ser representado como um sistema de primeira ordem, pois as duas respostas são idênticas.
</p>


<font size="2"><p style="text-align: center">Figura 29: Comparação do sistema de primeira e segunda ordem.</p></font>

## 8. Diagrama com detalhes dos protocolos de comunicaçãos entre os elementos.
<p style="text-align:justify;">
Até o momento no desenvolvimento da pesquisa, no circuito simulado e testado não temos protocolos de comunicação, pois, os dados são uniderecionados e o controle está relacionado com tensão. Foi identificado que estes protocolos de comunicação estão mais relacionados com a etapa de software que trabalhará com a coleta de dados e o processamento dos mesmos.
</p>

## 9. Testes Realizados de Eletrônica

<p style="text-align:justify;">Analisando o diagrama esquemático da figura 23 foi foram realizadas algumas simulações, as quais permitiram iniciar o processo de testes reais. O primeiro teste realizado foi foi realizado com um motor de passo, sendo assim testado o controle, que consistia em dar uma velocidade de giro por minuto, e medir com um cronômetro que efetivamente, o giro estava acontecendo no tempo programado, para realizar este controle, foi considerado que o motor NEMA 17, da 200 passor para realizar um giro completo, isso equivale a 1,8 graus em cada passo, então em função desta carácterística foi feita a programação, a figura 30 apresenta este teste realizado, esta imagem corresponde a um print do vídio que mostra o teste, o qual também é encontrado no  link: https://drive.google.com/file/d/17S0KqP9jFBvWxs0SBKxmJ0b5pLKGv4TY/view?usp=drive_link.</p>



<font size="2"><p style="text-align: center">Figura 30: Funcionamento de um motor de passo.
Fonte <a href="#ref-5"> [Própria]</a>.</p></font>

<p style="text-align:justify;">A figura 30 apresenta o motor de passo com o controle proposto, foram feitos vários testes, programando diferentes velocidades de giro e monitoradas com o cronômetro de um celular, foi verificado que os resultados obtidos eram iguais aos simulados.</p>

<p style="text-align:justify;">Assim, após ter testado o controle, foi modificado o código para poder controlar dois motores de passo com o mesmo código, porém com velocidades diferentes, pois, um motor vai controlar a mesa giratória e o outro a subida e descida da câmera e estes possivelmente tem velocidades diferentes, assim, usando um driver A4988 para cada motor foi testado  o controle projetado. O modelo real é mostrado na imagem 31, retirada da gravação do funcionamento dos motores, este teste pode ser visto no link: https://drive.google.com/file/d/14f_WduWOIXEFRaSpRaQQ2b-iNbAaqliE/view?usp=drive_link </p>



<font size="2"><p style="text-align: center">Figura 31: Modelo real dos motores.
Fonte <a href="#ref-5"> [Própria]</a>.</p></font>

<p style="text-align:justify;"> Na figura 31, observam-se os dois motores funcionando conforme o controle estabelecido. Um motor foi programado para completar uma volta em um minuto, enquanto o segundo realiza duas voltas em dois minutos. Apesar de a velocidade dos motores ser baixa, ela ainda não foi ajustada, pois depende da precisão na coleta de dados para realizar o escaneamento. Um motor controlará a rotação da mesa, enquanto o outro gerenciará a subida e descida da câmera responsável pela coleta de dados. A equipe de software ainda está estudando a definição da velocidade dos motores, mas essa alteração afetará apenas o código, sem necessidade de modificações na parte física do sistema.</p>

<p style="text-align:justify;">Seguidamente, foi realizado um teste de funcionamento do sensor de distância VL53L0X, o qual foi conectado nos pinos A4 e A5 da placa Arduino, a programação inicial foi realizada numa placa diferente, e testado unicamente o sensor de distância com o objetivo de evitar algum erro no sistema que já estava funcionando sem este sendor, a figura 32 apresenta à adição do sensor ao projeto. </p>



<font size="2"><p style="text-align: center">Figura 32: Adição do sensor de distância VL53L0X ao projeto.
Fonte <a href="#ref-5"> [Própria]</a>.</p></font>

<p style="text-align:justify;">A figura 33 foi tomada do vídio mostrado no link: https://drive.google.com/file/d/1DtzjjceVwn9kpxWSSLKbYMt8SEXWPkZC/view?usp=drive_link, que mostra o teste do sensor de distância e o resultado que ele apresenta no porto serial. O objetivo de uso deste sensor é para  realizar uma integração entre a parte de eletrônica, energia e Software, o sensor foi testado  para medir a distância do objeto que será colocado na mesa giratório, pois em função destes dados será realizado o escaneamento do objeto.</p>



<font size="2"><p style="text-align: center">Figura 33: Calibragem do sensor VL53L0X.
Fonte <a href="#ref-5"> [Própria]</a>.</p></font>

<p style="text-align:justify;">O programa de calibragem foi obtido dos exemplos fornecidos na biblioteca do Arduino para o sensor. O teste foi realizado da seguinte forma, foi colocada uma régua, como mostra a figura e programado o sensor, e seguidamente foi colocado um objeto na frente do sensor seguindo a numeração da régua, onde o sensor mostrava no porto serial a distância do objeto, é importante mencionar que este sensor mede até 2m, após esta distância ele mostra uma mensagem no porto serial de fora de rango de medida.</p>

<p style="text-align:justify;">Após finalizar esse teste de distância, os dois códigos (Motor e sensor de distância) foram combinados com o objetivo de mostrar no porto serial a velocidade dos motores e a distância captada pelo sensor. O objetivo é que o sensor detecte a distância do objeto na mesa e salve essas informações para posteriormente criar uma imagem a partir das distâncias coletadas, que serão processadas pela equipe de software, a figura 34 mostra o teste e ele pode ser assistido no link: https://drive.google.com/file/d/18fgzKlekGGNTxXlNJ5u1h-w8bg4Rdl3P/view?usp=drive_link .</p>



<font size="2"><p style="text-align: center">Figura 34: Sistema completo de teste.
Fonte <a href="#ref-5"> [Própria]</a>.</p></font>

<p style="text-align:justify;">A figura 34, mostra o circuito montado, esta imagem foi pega da gravação realizada do funcionamento dos motores e sensor, foi testada a mesmas velocidades dos motores e distância que media o sensor, os dados apareceram no porto serial conforme mostra a figura 35, onde se observa a distância registrada e a velocidade de cada motor.</p>



<font size="2"><p style="text-align: center">Figura 35: Saída de dados no porto serial.
Fonte <a href="#ref-5"> [Própria]</a>.</p></font>

<p style="text-align:justify;">Finaliza-se atualizando os digramas dos circuitos, com a versão que adiciona o sensor VL53L0X pois este não tinha sido considerado inicialmente no projeto, e surgiu em função da necessidade de integrar a parte de eletrônica com a parte de software, além disso, no vídeo mostrado no link: https://drive.google.com/file/d/1Eel66Ayi5QpEg17CPtpXBnag1mDMAQU4/view?usp=sharing, se mostra o controle final, onde o motor 1, gira dando uma volta por minuto, este motor vai controlar a mesa giratória, e motor 2 está parado, assim que o motor 1 termine de dar a volta o motor 2, da uma volta enteira em um segundo, isso para subir um step a câmera e dar inicio toma de uma segunda camada de dados, este processo é repetido até o sistema coletar todos os dados para serem processados.</p>



<font size="2"><p style="text-align: center">Figura 36: Diagrama esquemático com os motores e sensor de distância.
Fonte <a href="#ref-5"> [Própria]</a>.</p></font>



<font size="2"><p style="text-align: center">Figura 37: Diagrama de barramentos com os motores e sensor de distância.
Fonte <a href="#ref-5"> [Própria]</a>.</p></font>

## 10. Testes futuros

- Medir a corrente do sistema final, e a corrente proveniente da bateria para dimensionar os condutores (Motor) pois eles podem ter picos de até 2A;

- Repetido os testes com a mesa montada, com o objetivo de analisar o torque máximo com o peso máximo que a mesa poderá girar.

- Ajuste das tensões dos sensores, pois o Arduino precisa de 5V, o A4988 de 5V os motores de 12V e o sensor de distância VL53L0X funcionou adequadamente com 3.3V, para este caso sugiro usar as baterias de 12V e uma fonte que fornece 5 e 3,3V e garante uma corrente baixa para evitar danificar os sensores.

## Referências Bibliográficas

<div id="ref-1" />
[1] Curto circuito, introdução ao motor de passo, https://curtocircuito.com.br/blog/motor-de-passo/introducao-ao-motor-de-passo,acesso 19:04 hora: 13:17

<div id="ref-2" />
[2] FPG Paratodos, Controle de motor de passo,http://fpgaparatodos.com.br/2012/03/30/controle-de-um-motor-de-passo/ acesso 19/04/2024 hora 13:16

<div id="ref-3" />
[3] STA, Sistema de Tecnología aplicada, Ronteck,CARACTERÍSTICAS PRINCIPAIS DO ARDUINO UNO,https://www.sta-eletronica.com.br/artigos/arduinos/caracteristicas-principais-do-arduino-uno, Acesso, 12/04/2024 hora 16:00

<div id="ref-4" />
[4] O que é PWM e Para que Serve?,  Cristiano Bertulucci Silveira, publicado: novembro 26th, 2016, citisystems, acesso 16/04, hora 13:28, https://www.citisystems.com.br/pwm/
</a>

<div id="ref-5" />
[5] Robocore, PonteH,https://www.robocore.net/tutoriais/motor-dc-arduino-ponte-h-l298n, Acesso 16/04/2024, hora 13:33.

<div id="ref-6" />
[6] Datasheet - L298 - Dual full-bridge driver, https://www.st.com/resource/en/datasheet/l298.pdf

<div id="ref-7" />
[7] Smart kits blog,https://blog.smartkits.com.br/pwm-como-usar/#:~:text=O%20PWM%20opera%20controlando%20o,%2C%20consequentemente%2C%20a%20pot%C3%AAncia%20el%C3%A9trica, Acesso, 16/04/2024, hora 13:26 

<div id="ref-8" />
[8] Casa da Robótica, egulador de Tensão Step Down - Buck Conversor DC DC LM2596 3A, https://www.casadarobotica.com/fonte-e-conversores/conversores-dc-dc/step-down/regulador-de-tensao-step-down-buck-conversor-dc-dc-lm2596-3a, acesso 26/04/2024, hora: 20:25.

<div id="ref-8" />
[9] Maker Hero, Driver Motor de Passo A4988, https://www.makerhero.com/produto/driver-motor-de-passo-a4988/, acesso 03/06/2024, hora 18:00

<div id="ref-8" />
[10] Usando Múltiplos Sensores de Distância Laser VL53L0X, https://blog.smartkits.com.br/usando-multiplos-sensores-de-distancia-laser-vl53l0x/, acesso 01/06/2024 hora: 2:20

<div id="ref-8" />
[11]  ROJETO COM SENSOR DE DISTÂNCIA VL53L0X E ARDUINO PARA ALTA PRECISÃO, https://www.usinainfo.com.br/blog/projeto-com-sensor-de-distancia-vl53l0x-e-arduino-para-alta-precisao/, acesso 01/06/2024 hora: 2:20

## Tabela de versionamento

| Versão| Data | Descrição | Responsável|
|---|---|---|---|
| 1.0 | 03/05/2024 | Subindo o arquivo com dados do motor de passo | Miguel Munoz |
| 1.2 | 03/05/2024 | Atualização do documento de acordo com o template | Miguel Munoz |
| 1.3 | 03/05/2024 | Revisão da Diretoria Técnica para padronização | Carolina |
| 1.4 | 04/05/2024 | Ajustes de fontes e alinhamentos | Ana Carolina |
| 1.5 | 04/05/2024 | Atualização da formatação | Carolina |
| 2.0 | 05/06/2024 | Atualização das imagens | Miguel |
| 2.1 | 05/06/2024 | Ajuste do texto e numeração das imagens | Miguel |
| 2.2 | 06/06/2024 | Finalização da Informação de Eletrônica | Miguel |
| 2.3 | 07/06/2024 | Atualização da formatação e revisão do texto | Carolina |

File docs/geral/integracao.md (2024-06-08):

# Integração dos subsistemas

<p style="text-align: justify;">
O projeto ScanPoint envolve a integração de componentes eletrônicos, software e estrutura física para criar um sistema de escaneamento preciso e eficiente. 

Na parte eletrônica, o sistema é composto por dois motores de passo, dois drivers A4988 e um sensor de distância a laser VL53L0X, que trabalham em conjunto para controlar os movimentos do scanner. 

O software desempenha um papel crucial no processamento dos dados capturados pelo sensor. Utilizando comunicação via porta serial, os dados de distância são enviados para serem analisados e convertidos em um modelo digital tridimensional. Este processo requer algoritmos sofisticados para assegurar a precisão e a fidelidade da malha gerada em relação ao objeto escaneado.

A estrutura física do scanner é projetada para acomodar todos os componentes eletrônicos de maneira organizada e eficiente. É essencial que a estrutura ofereça um acesso adequado ao componentes eletrônicos e mantenha uma estética limpa, escondendo a fiação. A precisão no design da estrutura é fundamental para garantir que os movimentos dos motores sejam suaves e coordenados, permitindo uma análise detalhada e sem erros do objeto.
</p>

## Estrutura e energia

<p style="text-align: justify;">
A integração dos subsistemas de energia e estrutura do projeto consiste na construção de uma caixa para abrigar componentes dos subsistemas de energia e eletrônica. Feita em madeira MDF, os componentes estarão
apoiados diretamente neste material, já que o mesmo possui baixa condutividade.
Assim como as baterias, os barramentos e cabos também estarão fixados na caixa, para evitar um possível curto-circuito causado pelo contato desses componentes.

Visando a construção de um protótipo mais compacto, a escolha das baterias foi pensada para não ocupar muito espaço e não pesar sobre a estrutura. Além disso, a caixa foi projetada de forma a abrigar a quantidade atual de baterias com possibilidade incluir mais baterias a fim de estender o tempo de funcionamento do escaner.
</p>

## Estrutura e eletrônica

<p style="text-align: justify;">
A área de eletrônica se integra à área estrutural por ser importante conhecer o peso, tamanho e características dos componentes para que a equipe possa projetar e montar corretamente o sistema.

A parte eletrônica precisa de um espaço ventilado para acomodar a placa que conterá os sensores e motores,devendo ser algo considerado para evitar o superaquecimento dos componentes. Além disso, a equipe deve prezar pela estética, escondendo a fiação dentro da estrutura.

Quanto aos motores, a integração deles com a estrutura do scanner deve permitir um controle suave e coordenado dos movimentos, garantindo a precisão necessária na análise dos dados rotacionais e de elevação do sensor. Essa precisão é crucial para minimizar erros e assegurar que o objeto escaneado corresponda fielmente à malha gerada.

O funcionamento dos motores é o seguinte:

O motor 1 controla o prato, conforme mostrado na Figura 1, onde será colocado o objeto a ser escaneado. O motor 1 gira a uma volta por minuto, realizando 200 passos de 1,8 graus cada para completar uma rotação completa.
</p>

Integracao1

<div align="center">
    Figura 1 - Prato acoplado ao Motor 1
</div>
<br />

<p style="text-align: justify;">
O motor 2, que estará acoplado a uma barra de giro conforme mostrado na Figura 2, permanecerá parado até que o motor 1 complete sua rotação. Assim que o motor 1 finalizar sua volta, o motor 2 realizará um giro completo em 1 segundo. A função deste motor é elevar a câmera que fará o escaneamento, movimentando-se em passos de um minuto. Na câmera, estará instalado o sensor de distância a laser VL53L0X, responsável por medir a distância entre o objeto e a câmera.
</p>

Integracao2

<div align="center">
    Figura 2 - Acoplamento do Motor 2 a barra que subirá a câmera
</div>
<br />

<p style="text-align: justify;">
O Sensor de distância enviará os dados utilizando o porto serial da placa Arduino uno, para ser processados pela equipe de software, que gerará o arquivo para ser impresso pela impressora 3D.
</p>

## Energia e eletrônica

<p style="text-align: justify;">
O subsistema de energia é responsável por fornecer as tensões e correntes adequadas para alimentar os componentes do subsistema de eletrônica. Com isso em mente, a montagem de ambos os subsistemas foi realizada já considerando a fase de integração. Foram instalados conectores no final do subsistema de energia, os quais podem ser conectados diretamente ao Arduino e à Ponte H, recebendo, respectivamente, 12 V e 5 V.
</p>

## Software e eletrônica

<p style="text-align: justify;">
Como definido na arquitetura, a comunicação entre o Software e eletrônica está sendo feito a partir da entrada serial. Com isso, a aplicação em Electron se comunicará com o Arduíno pela entrada USB conectada diretamento no computador, sendo a conexão bidirecional, isto é, tanto o arduíno recebe sinais da aplicação, como a aplicação também recebe sinais do Arduíno.

Assim, a comunicação é dividida em dois pontos, a inicialização do processo de escaneamento e a comunicação das medições do Sensor infravermelho.
</p>

### Inicialização

<p style="text-align: justify;">
Para que o arduíno possa começar a fazer o processo de medição, ele precisará receber um sinal da aplicação, chamando assim, o loop de escaneamento.

Com isso o código para a comunicação é dividido no envio da mensagem pela aplicação e no recebimento dessa informação:
</p>

- Envio da mensagem: A aplicação deve instânciar um Port, definindo o baudRate, em seguida, chama um port.write com a mensagem a ser mandada ao Arduíno.

- Recebimento da mensagem: Após instânciar o Serial, faz a leitura dessa mensagem até identificar o fim da mensagem, ao receber a mensagem de início, se chama o código para leitura;

### Medição do Sensor

<p style="text-align: justify;">
Para fazer o processo de escaneamento e processamento da nuvem de pontos, os dados coletados pelo arduíno devem ser transmitidos para a aplicação, esse processo é mais simples, sendo necessário apenas que a aplicação leia o que o Arduíno está implimindo na entrada serial, usando o Serial.println(), na aplicação, após instânciar o port, podemos usar o parser-readline para ler os dados da entreda serial, assim recebendo os dados e processando-os como necessário na aplicação.
</p>

# Tabela de versionamento
|Versão| Data | Responsável | Descrição|
|---|---|---|---|
| 0.1 | 07/06/2024 | Carla R. Cangussú | Esqueleto do documento |
| 0.2 | 07/06/2024 | Artur de Sousa | Adicionado integração software e eletrônica |
| 0.3 | 07/06/2024 | Maria Claudia e Carolina | Adicionado integração estruturas e energia |
| 0.4 | 07/06/2024 | Carolina | Adicionado integração energia e eletrônica |
| 0.5 | 07/06/2024 | Brenda | Ajustes |

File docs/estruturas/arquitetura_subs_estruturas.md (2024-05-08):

# Arquitetura do Subsistema de Estruturas

<p style="text-align: justify;">
A Estrutura física do projeto ScanPoint foi pensada para comportar, de forma eficiente, todos os componentes eletrônicos do sistema. Para isso, o protótipo foi dividido em quatro subsistemas: estrutura de alumínio, prato giratório, elevação do sensor e a caixa da eletrônica (empacotamento da eletrônica). 
</p>

Diagrama de componentes da arquitetura de estruturas

<p style="text-align:center;">
Figura 1 - Diagrama de componentes da arquitetura de estruturas <br />
Fonte: Autores.
</p>

## Estrutura de alumínio

<p style="text-align: justify;">
Para a parte estrutural externa, foi pensado o uso de 12 perfis de alumínio estrutural, com dimensões de 20mmx20mm e comprimento de 700mm, ligados entre si por meio de cantoneiras e conjuntos de parafusos M4 com o auxílio de porca martelo. Assim formando uma estrutura em formato cuco, sendo os perfil as arestas, dando o apoio necessário para os demais subsistemas. 
</p>

Estrutura de alumínio

<p style="text-align:center;">
Figura 2 - Estrutura externa de alumínio <br />
Fonte: Autores.
</p>

Cantoneiras

<p style="text-align:center;">
Figura 3 - Cantoneiras utilizadas na fixação de estruturas <br />
Fonte: Autores.
</p>

## Caixa para eletrônica

<p style="text-align: justify;">
A Caixa da eletrônica foi pensada para armazenar todos os componentes eletrônicos do projeto como bateria, motor, componentes de controle como o Arduino, PCBs, cabos e demais equipamentos. Ela foi pensada de forma a otimizar o espaço de acordo com os componentes preliminares, esconder componentes cimo cabos e fios, dando melhor acabamento ao projeto, assim como deixar espaço suficiente para possíveis atualizações de eletrônica, energia ou software.
</p>

Caixa de eletrônica

<p style="text-align:center;">
Figura 4 - Caixa utilizada para o armazenamento dos componentes de eletrônica <br />
Fonte: Autores.
</p>

## Elevação do sensor

<p style="text-align: justify;">
O subsistema de elevação do sensor é feito com o auxilio de peças em impressão 3D, uma barra roscada fuso, barras guias, motor de passo, e o sensor de distância. Tais peças em impressão 3D são feitas em PLA, facilitando sua fabricação e servem como suportes para os demais componentes do subsistema. A elevação do sensor acontece através uma peça guiada por 2 eixos e sua movimentação ocorre a partir da barra fuso ligado ao motor de passo. 
</p>

Trilho do sensor

<p style="text-align:center;">
Figura 5 - Trilho para movimentação do sensor <br />
Fonte: Autores.
</p>

## Prato giratório

<p style="text-align: justify;">
O prato giratório servirá para auxiliar na movimentação da peça em questão que estará sendo escaneada. Ele foi projetado de acordo com os requisitos de tamanho da peça e peso máximo, além de possuir suporte para fixação do motor e apoio com roldanas para aumento de estabilidade durante a sua movimentação.
</p>

<!--<center><img src="docs/estruturas/imagens/Arquitetura_Estruturas_prato.jpg"></center>-->
Prato

<p style="text-align:center;">
Figura 6 - Prato utilizado para a rotação do objeto a ser escaneado <br />
Fonte: Autores.
</p>

## Versionamento
| Versão | Data | Modificação | Autor |
|--|--|--|--|
| 0.1 | 25/04/2024 | Criação do documento | Maria Claudia |
| 0.2 | 30/04/2024 | Adicionando textos e imagens | Maria Claudia e Diogo|
| 1.0 | 30/04/2024 | Atualização de drawings |Diogo|

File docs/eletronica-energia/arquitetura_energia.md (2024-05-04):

# Arquitetura do Subsistema de Energia

<p style="text-align:justify;"> A energia elétrica necessária para a operação do produto ScanPoint será fornecida por duas baterias de chumbo-ácido, todo o sistema estará operando em corrente contínua. As baterias fornecerão energia para as cargas (um  microcontrolador, um sensor de infravermelho e dois módulos L298N). Os motores, necessários para a rotação da mesa e movimentação do sensor de infravermelho, receberão energia de forma indireta, o módulo L298N estará sendo alimentado e assim alimentando os motores. Dessa forma, temos o seguinte diagrama representando a arquitetura: </p>

Diagrama_Energia

<font size="2"><p style="text-align: center">Figura 1 - Arquitetura de Energia. Fonte: Autoria própria <a href="#ref-1"> [1]. </a></p></font>

## Tabela de versionamento

| Versão| Data | Descrição | Responsável|
|---|---|---|---|
| 1.0 | 28/04/2024 | Criação do documento | Lucas Pantoja |
| 1.1 | 29/04/2024 | Edição de texto e imagem | Lucas Pantoja |
| 1.2 | 03/05/2024 | Atualização para padronização do documento| Lucas Pantoja |
| 1.3 | 04/05/2024 | Ajustes de alinhamento e formatação | Ana Carolina |

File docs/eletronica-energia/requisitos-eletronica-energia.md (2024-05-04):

## Requisitos do Subsistema

<p style="text-align:justify;">
Os requisitos adotados para o subsistema foram selecionados para garantir um funcionamento eficiente, confiável e seguro do scanner de forma que atenda plenamente às necessidades dos usuários.
</p>
<font size="2"><p style="text-align: center">Tabela 1 - Requisitos Funcionais (RF)</p></font>

| Requisito | Nome | Descrição |
|:---:| :--- |:---:|
| RF01 | Integração do Motor e Controle de Velocidade | Desenvolver um sistema de controle para o motor da mesa giratória que permita manter a velocidade de rotação e parar a rotação conforme necessário durante o escaneamento do objeto.
| RF02 | Integração do Motor e Altura do Sensor | Desenvolver um sistema de controle para o motor do sistema de regulação de altura do sensor de distância infravermelho.
| RF03 | Comunicação com o Software | Implementar um sistema de comunicação entre o controle dos motores e da iluminação com o software de escaneamento.
| RF04 | Alimentação do Sistema | Projetar um sistema de alimentação elétrica que fornece energia estável e adequada para todos os componentes eletrônicos do scanner, incluindo o motor, sensor de distância infravermelho e circuitos de controle.

<p style="text-align:justify;">
Os requisitos funcionais (RF) abrangem a integração de um motor com o controle de velocidade, permitindo a manutenção e ajuste da velocidade de rotação, bem como a possibilidade de interromper a rotação conforme necessário durante o escaneamento do objeto. Além disso, inclui-se a integração de um segundo motor com o sistema de regulação de altura do sensor de distância infravermelho, assegurando uma adaptação precisa do sensor em relação ao objeto durante o processo de escaneamento. A implementação de um sistema de comunicação entre o controle dos motores e a iluminação com o software de escaneamento também é um requisito funcional crucial. 
</p>

<font size="2"><p style="text-align: center">Tabela 2 - Requisitos Não Funcionais (RNF)</p></font>

| Requisito | Nome | Descrição |
|:---:| :--- |:---:|
| RNF01 | Eficiência Energética | Selecionar componentes e desenvolver algoritmos de controle que otimizem o consumo de energia do sistema, maximizando a eficiência energética e minimizando o desperdício de energia.
| RNF02 | Compatibilidade com Normas de Segurança | Seguir as normas de segurança elétrica relevantes para garantir a segurança dos usuários e a conformidade com regulamentações aplicáveis.
| RNF03 | Tempo de Resposta | Garantir um tempo de resposta rápido para as ações de controle do motor, minimizando a latência entre os comandos do software e as alterações na velocidade de rotação da mesa.
| RNF04 | Durabilidade e Confiabilidade | Selecionar componentes de alta qualidade e projetar circuitos robustos para garantir a durabilidade e a confiabilidade do sistema, reduzindo a probabilidade de falhas durante o uso.
| RNF05 | Compatibilidade com Protocolos de Comunicação | Utilizar protocolos de comunicação padrão e amplamente suportados para garantir a interoperabilidade entre os diferentes 

<p style="text-align:justify;">
No que concerne aos requisitos não funcionais (RNF), destaca-se a priorização da eficiência energética para otimizar o consumo de energia do sistema, visando redução de custos operacionais e minimização de desperdício energético. A compatibilidade com normas de segurança elétrica é essencial para assegurar a proteção dos usuários e a conformidade com regulamentações, enquanto a garantia de um tempo de resposta rápido é crucial para uma operação ágil e responsiva do sistema. A durabilidade, confiabilidade e a compatibilidade com protocolos de comunicação são aspectos voltados a promover a estabilidade operacional, maximizando a vida útil do sistema e facilitando a integração entre os componentes eletrônicos.
</p>

## Versionamento

| Versão | Data | Descrição | Responsável |
|---|---|---|---|
| 0.1 | 21/04/2024 | Adição dos requisitos | Carolina |
| 0.2 | 26/04/2024 | Revisão conforme modificações acordadas pelo grupo | Carolina |
| 0.3 | 03/05/2024 | Adicionando desenvolvimento e corrigindo formatação | Carolina |
| 0.4 | 04/05/2024 | Ajustes de fontes | Ana Carolina |

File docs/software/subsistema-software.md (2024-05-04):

# Projeto de Subsistema de Software

## Arquitetura de Software
<p style="text-align: justify;">
A arquitetura do software está definida no diagrama abaixo, sendo dividido no aplicativo, no conversor, no embarcado, sensor infravermelho e dois motores:
</p>
diagrama arquitetura
<font size="2"><p style="text-align: center">Fonte: [Diagrama de Arquitetura de Software](https://app.diagrams.net/#G152ySAVfwL1QUKcdnSeAaXdJ9Q1nRN_6T#%7B"pageId"%3A"C2fSY1v2SiZeoUbDoYyL"%7D).</p></font>

<p style="text-align: justify;">
Para atingir os objetivo será utilizado três tecnologias: Electron, para o aplicativo, Python para o processamento da nuvem de pontos e Arduino, para o embarcado.
Mais detalhes na pagina de [Arquitetura de Software](arquitetura.md)
</p>

* **Aplicação ScanPoint:** A aplicação desktop será responsável pelo controle do processo de criação do STL. Ela que será responsável por chamar o software de processamento do pointcloud para a conversão para STL e interagir com o usuário final.

* **Arduino:** responsável por receber dados provenientes dos sensores, realizando o processamento necessário e transmitindo essas informações para a aplicação Electron. Além disso, assume o controle dos motores, gerenciando seu funcionamento e movimentação de acordo com as instruções fornecidas pela aplicação. No âmbito operacional, o Arduino opera como uma unidade mestra, coordenando e controlando o fluxo de dados entre os diferentes componentes do sistema. O arduíno foi selecionado por conta da versatilidade da placa, atendendo todas as necessidades com baixo custo e curva de aprendizado.

* **Script para processamento de pointcloud:** Responsável pela leitura dos pontos do objeto devolvidos pelo arduíno fazendo a modelagem do objeto através desses pontos, sendo assim, por fim, gerando o arquivo STL ou g-code.

## Interface

### Guia de estilo
<p style="text-align: justify;">
Foi desenvolvido um guia de estilo que irá elucidar sobre os padrões e no estilo da interface principal da aplicação que será desenvolvida em Electron.
Mais detalhes na pagina de [Documento de identidade](identidade.md)
</p>

### Protótipo de alta fidelidade
<p style="text-align: justify;">
Com sentido de orientar sobre o formato das telas e disposição de seus elementos como descrição de comportamento e interação da interface, foi desenvolvido um protótipo de alta fidelidade.
Mais detalhes na pagina de [Protótipo de alta fidelidade](prototipo.md)
</p>

### Tecnologia utilizada
<p style="text-align: justify;">
O Electron é um framework open-source para criar aplicações Desktop usando tecnologias web para Windows, mac e Linux, com base no Chromium e Node.js, com isso ele é um framework que utiliza linguagem e estrutura de mais fácil curva de aprendizado. Seu lançamento completa 10 anos o que já demonstra uma certa robustez, apesar de recente,ainda possui material para ser utilizado como base. <a href="#ref1">[1]</a>
</p>

## Script de processamento PointCloud
<p style="text-align: justify;">
Após a leitura de todos os pontos de distância feito pelos sensores ligados ao arduíno, o arquivo .txt gerado deve ser passado por um script de conversão desenvolvido em Python, usando a biblioteca NumPy, escolhido pela confiabilidade do python para as operações matemáticas.

No geral ele irá ler todos os valores de distância do arquivo txt e irá processar os dados, aplicando a distância do sensor ao ponto de leitura, transformar em uma matrix de rotação e depois em pontos cartesianos. Em seguida elimina todos os pontos fora de alcance do sensor e passa todos os valores para ser convertido em STL.
</p>

## Comunicação com arduíno
<p style="text-align: justify;">
A comunicação será feita principalmente, e unicamente, através de um cabo USB. Sendo mandado os sinais por parte da interface para interação com o scanner (exemplo: início do motor, ligar o infravermelho, e etc), como a transmissão, por parte do arduíno, do arquivo .txt contendo os pontos do objeto lidos pelo infravermelho.
</p>

## Software embarcado
<p style="text-align: justify;">
Pela parte embarcada será utilizada a linguagem C. Sendo feito o controle dos motores, leitura do infravermelho, gravação no arquivo .txt e envio.
</p>

## Referências
<div id="ref1"/>
>[1][What is Electron? Acesso em 28 de abril de 2024.](https://www.electronjs.org/docs/latest/)

<div id="ref2"/>
>[2] [Diagrama de arquitetura de software. Acesso em 03 de abril de 2024.](https://app.diagrams.net/#G152ySAVfwL1QUKcdnSeAaXdJ9Q1nRN_6T#%7B"pageId"%3A"C2fSY1v2SiZeoUbDoYyL"%7D..)

## Tabela de versionamento

| Versão| Data | Descrição | Responsável|
|---|---|---|---|
| 0.1 | 29/04/2024 | Criação do documento | Artur Vieira |
| 0.2 | 30/04/2024 | Adição da comunicação com arduíno | Guilherme Basílio |
| 0.3 | 30/04/2024 | Adição da tecnologia utilizada | Ciro Araújo |
| 0.4 | 02/05/2024 | Formatação e adição do software embarcado | Denniel William |
| 0.5 | 04/05/2024 | Mudança de titulo do documento e erros de portugues | Ana Carolina |

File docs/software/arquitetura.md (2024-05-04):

# Arquitetura de Software

<p style="text-align: justify;"> Esta sessão elenca todos os itens de arquitetura de software, como os componentes utilizados, sua comunicação e as tecnologias utilizadas.
</p>

## Componentes 
<p style="text-align: justify;">
A arquitetura de software está dividida nos seguintes componentes:
</p>

- Aplicação: Desenvolvida em Electron, cuida de toda a interação com usuário e sinais para comunicação com o embarcado. Ela possui um front-end com opções iterativas para o usuário controlar o sistema;
- Script de conversão: Vai converter o arquivo de texto com as informações espaciais do objeto e transformar em .stl(formato para impressão 3D)
- Embarcado: Usando uma Arduino, ela faz a comunicação com os componentes do sistema e retorna o arquivo de texto com os dados espaciais do objeto;
- Sensor Infravermelho: Irá fazer a leitura de distâncias, mapeando o objeto;
- Motor de rotação: Irá girar a mesa onde o item está posicionado, possibilitanto a leitura do objeto em 360 graus;
- Motor de regulação de altura: Irá possibilitar a regulação da altura do sensor infravermelho, assim passando por todo o comprimento do objeto;

<p style="text-align: justify;">
A relação entre os componentes está elencada no diagrama abaixo:
</p>

## Metas e Restrições Arquiteturais
### Metas
- O aplicativo deve ser de fácil utilização
- O aplicativo deve garantir o escaneamento do objeto posto na mesa
- O aplicativo não precisa de conexão a internet
- O aplicativo deve desempenhar suas funções de forma eficiente

### Restrições
- A aplicação deverá ser disponibilizada por meio um aplicativo de computador
- É necessário possuir um desktop ou notebook para utilização.
- Para funcionamento pleno ele deve estar conectado ao scanner.
- Deve ser desenvolvida em JavaScript (Interface), Python(Processamento de pontos de nuvem) e C(Sistema embarcado).

## Diagrama de arquitetura de software 



<font size="2"><p style="text-align: center">Fonte: [Diagrama de Arquitetura de Software](https://app.diagrams.net/#G152ySAVfwL1QUKcdnSeAaXdJ9Q1nRN_6T#%7B"pageId"%3A"C2fSY1v2SiZeoUbDoYyL"%7D).</p></font>

## Tecnologias

<p style="text-align: justify;">
AS tecnologias de software utilizadas nesse projeto foram:
</p>

- Electron: É um framework open-source para criar aplicações Desktop usando tecnologias web para Windows, mac e Linux, com base no Chromium e Node.js; <a href="#ref1">[1]</a>

- Arduino: É uma plataforma open-source com hardware e software com fácil aprendizagem. As placas Arduino tem a capassidade de registrar entradas diferentes, como botões, sinais de sensores, etc. Para programar as placas, existe o Arduino IDE (que é multiplataforma), com sua própria linguagem de programação. <a href="#ref2">[2]</a>

## Visão de caso de uso

<p style="text-align: justify">Seguindo um nível maior de abstração em comparação a outros tópicos tratados no documento, a visão de casos de uso visa auxiliar no entendimento das interações dos atores com o sistema de forma a descrever os cenários de uso da aplicação. Para mais detalhes sobre o caso de uso o documento está disponível em [caso de uso](casos-de-uso.md).</p>

<iframe frameborder="0" style="width:100%;height:300px;" src="https://viewer.diagrams.net/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"></iframe>
<font size="2"><p style="text-align: center">Figura 1: [Diagrama Casos de Uso](https://viewer.diagrams.net/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).</p></font>

## Visão Lógica
### Visão Geral
<p style="text-align: justify;">As visões de uma determinada arquitetura são abstrações dos modelos já criados para o projeto. Na ocasião da visão lógica, o objetivo é decompor os subsistemas e seus respectivos pacotes, apresentando as suas principais características, a fim de melhorar a qualidade de qualquer documento de modelagem já elaborado. O objetivo não é entrar em muitos detalhes por ser responsabilidade da própria modelagem e dos documentos criados para cada aspecto.</p> 

### Diagrama de pacotes
O diagrama de pacotes descreve a estrutura de pastas e módulos divididos para interface. Abaixo segue o diagrama de pacotes referente a interface, para mais detalhes acesse [diagrama de pacotes](diagrama-de-pacotes.md).

<iframe frameborder="0" style="width:100%;height:400px;" src="https://viewer.diagrams.net/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"></iframe>
<font size="2"><p style="text-align: center">Figura 1: [Diagrama de Pacotes](https://viewer.diagrams.net/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).</p></font>

## Referências
<div id="ref1"/>
>[1][What is Electron? Acesso em 28 de abril de 2024.](https://www.electronjs.org/docs/latest/)

<div id="ref2"/>
>[2] [What is Arduino? Acesso em 28 de abril de 2024.](https://docs.arduino.cc/learn/starting-guide/whats-arduino/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..)

<div id="ref3"/>
>[3] [Diagrama de arquitetura de software. Acesso em 03 de abril de 2024.](https://app.diagrams.net/#G152ySAVfwL1QUKcdnSeAaXdJ9Q1nRN_6T#%7B"pageId"%3A"C2fSY1v2SiZeoUbDoYyL"%7D..)

## Tabela de versionamento

| Versão| Data | Descrição | Responsável|
|---|---|---|---|
| 1.0 | 28/04/2024 | Criação da estrutura do documento | Artur de Souza |
| 1.1 | 03/05/2024 | Atualização do documento | Denniel William |
| 1.2 | 03/05/2024 | Corrigido Formatação | Artur de Souza |
| 1.3 | 03/05/2024 | Adicionando referencia e legenda ao diagrama | Guilherme Basilio |

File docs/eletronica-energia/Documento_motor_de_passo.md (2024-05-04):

# Projeto do Subsistema de Eletrônica

<p style="text-align:justify;">
O subsistema eletrônico desempenha o papel de controle sobre os motores, comunicação com o software, integração dos sensores. Nesse contexto, o foco da equipe consistiu na seleção dos componentes eletrônicos e na implementação de estratégias de gerenciamento em conformidade estrita com as normas de segurança elétrica pertinentes.
</p>

## Motor de Passo

<p style="text-align:justify;">
O Motor de Passo é um motor elétrico utilizado para controle de movimentos de forma precisa, este controle é feito através de passos ou graus, com isso é possível controlar o motor sem o uso de sensores para determinar posição. Os motores desse tipo são controlados através de sinais digitais enviados para as suas bobinas, possibilitando a rotação fracionada do eixo, sem a necessidade de escovas internas <a href=“../eletronica-energia/Projeto_do_Subsistema_de_Energia.md#ref-1“> [1]</a>.
</p>

### Estrutura do Motor de Passo
<p style="text-align:justify;">
As características do Motor de Passo, no que diz respeito à velocidade, torque e resolução são definidas primeiramente pela estrutura do motor, então é importante conhecer os aspectos internos e a função das peças que compõem o motor.
</p>



<font size="2"><p style="text-align: center">Figura 1: Estrutura interna do motor de passo <a href=“../eletronica-energia/Projeto_do_Subsistema_de_Energia.md#ref-1“> [1]. </a></p></font>

#### Rotor
<p style="text-align:justify;">
Uma das partes mais importantes do motor de passo é o rotor, na Figura 1, é mostrado  um motor com rotor híbrido, o corpo que representa o rotor híbrido é composto pelos dois rotores e o imã entre eles, utilizado para a polarização do rotor frontal e o traseiro <a href=“../eletronica-energia/Projeto_do_Subsistema_de_Energia.md#ref-1“> [1]</a>.

Existem três configurações possíveis de montagem para o rotor: rotor de imã permanente, rotor de relutância variável e rotor híbrido, o tipo híbrido é o mais comumente utilizado, estas diferenças são apresentadas na Tabela 1.
</p>

<font size="2"><p style="text-align: center">Tabela 1: Diferenças entre os rotores.</p></font>



#### Estator
<p style="text-align:justify;">
O Estator produz o campo magnético que causa a movimentação do rotor. Para análise do estator é necessário tomar nota de alguns pontos como: o número de fases, de par de polos e configuração do fio. A fase ou o par de polos é formado por duplas de bobinas que são energizadas simultaneamente.

A estrutura do estator é formada por polos magnéticos dentados, sendo que cada polo é dotado de uma bobina com o seu par oposto, de forma que os pares são energizados simultaneamente e por consequência são magnetizados com a mesma polaridade, os dois polos formam uma fase. 

O primeiro modelo do exemplo abaixo é do tipo estator bifásico, com fases A e B, enquanto o segundo é do tipo estator trifásico, com fases A, B e C.
</p>


<font size="2"><p style="text-align: center">Figura 2: Modelo de um estator bifásico.</p></font>


<font size="2"><p style="text-align: center">Figura 3: Estator real.</p></font>

<p style="text-align:justify;">
A Figura 2, mostra uma representação gráfica da distribuição das bobinas no estator, já a Figura 3, mostra uma imagem de um estator real, com seus dentes e bobinas em enrolamento de cobre.

O eixo do motor híbrido é construído com dois grupos dentados de rotores, um deles polarizados com polo sul e outro com polo norte.
</p>


<font size="2"><p style="text-align: center">Figura 4: Modelo do eixo do motor <a href=“../eletronica-energia/Projeto_do_Subsistema_de_Energia.md#ref-1“> [1]</a>.</p></font>

### Tipos de Polos
<p style="text-align:justify;">
Existem dois modelos de acordo com os polos, o bipolar e o unipolar, os termos surgiram de conformidade com os drivers que são utilizados para acionamento desses motores. O polar do termo representa “polaridade” e se refere ao driver utilizado para controle desses motores, utilizaremos as expressões “motor unipolar” e “motor bipolar” por convenção social <a href=“../eletronica-energia/Projeto_do_Subsistema_de_Energia.md#ref-1“> [1] </a>.
</p>
 
#### Unipolar
<p style="text-align:justify;">
O modelo utilizado com o driver Unipolar conta com duas bobinas por fase, formando um par de polos, além disso, há o contato em comum, dessa forma os motores desse tipo podem ter 5, 6 ou 8 fios <a href=“../eletronica-energia/Projeto_do_Subsistema_de_Energia.md#ref-1“> [1] </a>.
</p>



<font size="2"><p style="text-align: center">Figura 5: Driver unipolar <a href=“../eletronica-energia/Projeto_do_Subsistema_de_Energia.md#ref-1“> [1]</a>.</p></font>

<p style="text-align:justify;">
Com o fio central é possível controlar a direção da corrente, no entanto apenas metade da bobina pode ser utilizada, isso faz com que o motor seja menos eficiente se comparado ao bipolar. O fio central é conectado ao Vin do circuito, sendo que se o Mosfet 1 estiver ativo, a corrente fluirá de Am para A+, se o Mosfet ativo for o 2, a corrente fluirá de Am para A-.
</p>


<font size="2"><p style="text-align: center">Figura 6: Diagrama circuito unipolar <a href=“../eletronica-energia/Projeto_do_Subsistema_de_Energia.md#ref-1“> [1] </a>.</p></font>

#### Bipolar
<p style="text-align:justify;">
No motor do tipo bipolar, cada bobina é composta por dois fios apenas, sem derivações centrais como as do tipo unipolar, de forma que são motores mais fáceis de serem produzidos.
</p>



<font size="2"><p style="text-align: center">Figura 7: Driver bipolar <a href=“../eletronica-energia/Projeto_do_Subsistema_de_Energia.md#ref-1“> [1]</a>.</p></font>

<p style="text-align:justify;">
Como não há a derivação central, para controle de direção é necessário utilizar uma ponte H, exigindo um circuito de acionamento mais complexo. Para os motores desse tipo, temos que a corrente flui de A- para A+ quando os Mofets 2 e 3 estão ativos, e flui de A+ para A- quando 1 e 4 estão ativos. Apesar de possuir um acionamento mais complexo, os motores do tipo bipolar são mais comuns, pois permitem que o motor atinja maior torque <a href=“../eletronica-energia/Projeto_do_Subsistema_de_Energia.md#ref-1“> [1]</a>.
</p>



<font size="2"><p style="text-align: center">Figura 8: Diagrama circuito bipolar <a href=“../eletronica-energia/Projeto_do_Subsistema_de_Energia.md#ref-1“> [1]</a>.</p></font>

### Funcionamento de um motor de passo:
<p style="text-align:justify;">
O motor de passo é um dispositivo eletromecânico composto por bobinas (indutores) e um rotor magnético (ímã permanente ou imantado). As bobinas convertem energia elétrica em campo magnético, alinhando o rotor a esse campo. A excitação correta das bobinas faz o rotor, que gira em torno de seu eixo, mover-se no sentido desejado, convertendo energia magnética em movimento (energia mecânica). O rotor é rotacionado em pequenos incrementos angulares, chamados de "passos" <a href=“../eletronica-energia/Projeto_do_Subsistema_de_Energia.md#ref-2“> [2]</a>.

O funcionamento básico do motor de passo envolve o uso de bobinas alinhadas dois a dois. Quando energizadas, elas atraem o rotor, alinhando-o com o campo magnético gerado, resultando em uma variação angular pequena, chamada de passo. A velocidade e o sentido de movimento são determinados pela forma como cada bobina é ativada, incluindo a ordem e a velocidade entre cada processo de ativação <a href=“../eletronica-energia/Projeto_do_Subsistema_de_Energia.md#ref-2“> [2]</a>.

As vantagens do motor de passo incluem sua precisão de posicionamento e torque aplicado, além de ter uma resposta excelente na aceleração e desaceleração, devido à sua lógica digital. No entanto, ele pode apresentar baixo desempenho em alta velocidade, requer um certo grau de complexidade para operação e pode sofrer ressonância devido a um controle inadequado <a href=“../eletronica-energia/Projeto_do_Subsistema_de_Energia.md#ref-2“> [2]</a>.

Complementando com o banco de dados, o motor de passo é frequentemente utilizado em aplicações que exigem precisão de posicionamento, como impressoras 3D, máquinas CNC e robótica industrial. Ele oferece um controle preciso sobre o movimento, o que é essencial em muitas aplicações. Além disso, o motor de passo pode ser facilmente controlado por microcontroladores, o que o torna uma escolha popular em projetos eletrônicos e de automação <a href=“../eletronica-energia/Projeto_do_Subsistema_de_Energia.md#ref-2“> [2]</a>.

A figura a seguir mostra como um motor de passo pode ser controlado mediante lógica binária:
</p>
 

<font size="2"><p style="text-align: center">Figura 9: Motor de passo controlado pelas entradas To até T3 <a href=“../eletronica-energia/Projeto_do_Subsistema_de_Energia.md#ref-2“> [2]</a>.</p></font>

## Placa Arduino Uno
<p style="text-align:justify;">
O Arduino Uno é uma placa microcontrolada baseada no chip ATmega328. Esta placa é muito utilizada no desenvolvimento de projetos embarcados, é hoje em dia é a mais utilizada e documentada da família Arduino.
</p>

	 

<font size="2"><p style="text-align: center">Figura 10: Placa Arduino Uno, diagrama de barramento e diagrama esquemático. Fonte: Autoria própria.</p></font>

<p style="text-align:justify;">
A placa conta com um chip ATmega328 que é um microcontrolador único desenvolvido pela Atmel, pertencente à família megaAVR. A arquitetura do Arduino Uno segue o padrão Harvard e possui um núcleo de processador RISC de 8 bits customizado.
</p>



<font size="2"><p style="text-align: center">Figura 11: Diagrama de pinos da placa Arduino Uno <a href=“../eletronica-energia/Projeto_do_Subsistema_de_Energia.md#ref-3“> [3]</a>.</p></font>

### Características principais do Arduino Uno

 - A tensão de operação é 5V
 - A tensão de entrada recomendada varia de 7V a 12V
 - A tensão de entrada varia de 6V a 20V
 - 14 pinos de entrada/saída digital
 - 6 pinos analógicos
 - A corrente DC para cada pino de entrada/saída é de 40 mA
 - A corrente DC para o pino de 3,3 V é 50 mA
 - A memória flash é de 32 KB
 - SRAM é 2KB
 - EEPROM é 1 KB
 - A velocidade do CLK é de 16 MHz

### Diagrama de pinos do Arduino Uno
<p style="text-align:justify;">
A placa do Arduino Uno conta com uma grande variedade de pinos de alimentação, pinos analógicos, ATmega328, conector ICSP, botão Reset, LED de alimentação, pinos digitais, led de teste, pinos TX/RX, interface USB e fonte de alimentação externa, na Figura 12, se apresentam estes pinos.
</p>



<font size="2"><p style="text-align: center">Figura 12: Diagrama de Pinos do microcontrolador ATmega328.</p></font>

<p style="text-align:justify;">
A seguir se faz a descrição de cada um dos componentes do diagrama na Figura 12.
</p>

#### Descrições principais para utilização do Arduino Uno

##### Fonte de Alimentação
<p style="text-align:justify;">
Esta placa conta com uma grande vantagem e é poder ligar ela de forma externa com ajuda de um cabo USB ou uma fonte de alimentação externa, além disso, as fontes de alimentação externas incluem principalmente um conversor AC para DC, caso contrário, uma bateria. A fonte deve ser inserida no conector de alimentação da placa Arduino. Suas faxas de tensão estão entre 7 e 12 Volts,  conta com um pino GND e conector POWER <a href=“../eletronica-energia/Projeto_do_Subsistema_de_Energia.md#ref-3“> [3]</a>.
</p>

##### Entradas e saídas digitais
<p style="text-align:justify;">
O Arduino Uno possui 14 pinos que podem ser usados como entrada ou saída a depender da necessidade do programador. Com a ajuda de funções como pinMode(), digitalWrite() e Digital Read() é possível definir como os pinos serão utilizados <a href=“../eletronica-energia/Projeto_do_Subsistema_de_Energia.md#ref-3“> [3]</a>.
</p>

##### Entradas analógicas
<p style="text-align:justify;">
A placa Arduino UNO conta com 6 canais de conversor analógico para digital, nomeadas de A0 a A5. Sendo que a resolução do conversor analógico digital é de 10Bits. Isso significa que este irá mapear tensões entre 0 e a tensão operacional (5V ou 3.3V) para valores inteiros entre 0 e 1023. No Arduino UNO, isso permite uma resolução entre leituras de: 5 volts / 1024 unidades, ou .0049 volts (4.9 mV) por unidade. Essas entradas são nomeadas de A0 a A5. A função analogRead() lê o valor de um pino analógico especificado <a href=“../eletronica-energia/Projeto_do_Subsistema_de_Energia.md#ref-3“> [3]</a>.

#### Pino (TX) e Pino (RX) (Serial):
<p style="text-align:justify;">
Os pinos 0 e 1 são usados para transmitir e receber dados seriais TTL, e estes são conectados aos pinos equivalentes do chip ATmega8U2 USB para TTL Serial <a href=“../eletronica-energia/Projeto_do_Subsistema_de_Energia.md#ref-3“> [3]</a>.
</p>

#### Pinos externos de interrupção:
<p style="text-align:justify;">
Os pinos 2 e 3 do Arduino Uno podem desempenhar a função de entrada de sinal para interrupção externa tais funções são nomeadas de INT0 e INT1, respectivamente <a href=“../eletronica-energia/Projeto_do_Subsistema_de_Energia.md#ref-3“> [3]</a>.
</p>

#### Pinos 3, 5, 6, 9, 10 e 11 (PWM):
<p style="text-align:justify;">
O Arduino Uno possui 6 pinos para saída PWM, são estes os pinos 3, 5, 6, 9, 10 e 11. Para auxiliar na manipulação desses pinos a plataforma possui uma função que auxilia na escrita de valores chamada de “duty cycle” facilitando a utilização do PWM do Arduino Uno, o qual pode ser acoplado com módulos externos <a href=“../eletronica-energia/Projeto_do_Subsistema_de_Energia.md#ref-3“> [3]</a>.
</p>

#### Pinos SPI (Pino-10 (SS), Pino-11 (MOSI), Pino-12 (MISO), Pino-13 (SCK):
<p style="text-align:justify;">
SPI (Serial Peripheral Interface) é um protocolo de comunicação serial, a SPI possui uma conexão full duplex, o que significa que os dados são enviados e recebidos simultaneamente. O SPI pode ser utilizado para a comunicação entre dois arduinos <a href=“../eletronica-energia/Projeto_do_Subsistema_de_Energia.md#ref-3“> [3]</a>.
</p>

#### LED Interno Pino 13
<p style="text-align:justify;">
A placa do Arduino Uno possui um Led interno conectado ao pino 13 (pino digital). Como pino de valor ALTO, o diodo emissor de luz é ativado, sempre que o pino estiver em nível BAIXO <a href=“../eletronica-energia/Projeto_do_Subsistema_de_Energia.md#ref-3“> [3]</a>.
</p>

#### Pino-4 (SDA) e Pino-5 (SCL) (I2C):
<p style="text-align:justify;">
Permite comunicação TWI (Two Wire Interface) com a ajuda da biblioteca Wire <a href=“../eletronica-energia/Projeto_do_Subsistema_de_Energia.md#ref-3“> [3]</a>.
</p>

#### AREF (Tensão de Referência):
<p style="text-align:justify;">
AREF significa Referência Analógica. Ele permite alimentar o Arduino com uma tensão de referência de uma fonte de alimentação externa para configurar a tensão de referência usada para entrada analógica (ou seja, o valor usado como o topo da faixa de entrada) <a href=“../eletronica-energia/Projeto_do_Subsistema_de_Energia.md#ref-3“> [3]</a>.
</p>

#### Pino de Reset:
<p style="text-align:justify;">
Este pino é usado para resetar (RST) o microcontrolador <a href=“../eletronica-energia/Projeto_do_Subsistema_de_Energia.md#ref-3“> [3]</a>.
</p>
 
### Memória
<p style="text-align:justify;">
A memória do microcontrolador Atmega328 do Arduino Uno inclui memória flash de 32 KB para armazenamento de código, SRAM-2 KB e EEPROM-1 KB <a href=“../eletronica-energia/Projeto_do_Subsistema_de_Energia.md#ref-3“> [3]</a>.
</p>

### Comunicação
<p style="text-align:justify;">
O Arduino Uno ATmega328 oferece comunicação serial UART TTL e é acessível em pinos digitais como TX (1) e RX (0). O software de um Arduino possui um monitor serial que permite dados fáceis. Existem dois LEDs na placa, como RX e TX, que piscarão sempre que os dados estiverem sendo transmitidos através do USB.

A biblioteca SoftwareSerial permite a comunicação serial nos pinos digitais do Arduino Uno e o ATmega328P suporta TWI (I2C), bem como comunicação SPI. O software Arduino contém uma biblioteca cabeada para simplificar a utilização do barramento I2C <a href=“../eletronica-energia/Projeto_do_Subsistema_de_Energia.md#ref-3“> [3]</a>.
</p>

### Proteção de alta tensão do USB
<p style="text-align:justify;">
A placa Arduino Uno possui um fusível que protege a porta USB do PC de sobretensão. Embora a maioria dos PCs tenha sua própria proteção interna, o fusível oferece uma proteção adicional de segurança <a href=“../eletronica-energia/Projeto_do_Subsistema_de_Energia.md#ref-3“> [3]</a>.
</p>

### Características físicas
<p style="text-align:justify;">
As características físicas de uma placa Arduino incluem principalmente comprimento e largura. O comprimento e a largura da placa de circuito impresso do Arduino Uno são 2,7 X 2,1 polegadas, mas o conector de alimentação e o conector USB se estenderão além dessa medida. A placa pode ser fixada na superfície, caso contrário, com os orifícios dos parafusos <a href=“../eletronica-energia/Projeto_do_Subsistema_de_Energia.md#ref-3“> [3]</a>.
</p>

## Ponte H, Driver L298N
<p style="text-align:justify;">
Este componente facilita o projeto do controle PWM, por nele encontra-se toda a configuração de portas lógicas, transistores e capacitores para realizar a modulação, ele tem as seguintes especificações segundo o fabricante.
</p>

### Especificações

- Tensão de Operação: 4.5 V a 46 V
- Controle de 2 motores DC ou 1 motor de passo
- Corrente de Operação máxima: 2 A por canal ou 4 A total
- Tensão lógica: 4.5 V a 7 V
- Corrente lógica: 0 a 36 mA
- Limites de Temperatura: -20°C a +135°C
- Potência Máxima: 25 W
- Dimensões: 43 x 43 x 27 mm

<p style="text-align:justify;">
As pontes H  utilizam quatro transistores que, ao receber um sinal vindo do microcontrolador, permitem a passagem de corrente para os terminais do motor, fazendo com que ele rotacione no sentido desejado, esta ponde encontra-se no driver L298N utiliza duas pontes H para controlar separadamente dois motores. Porém, além de controlar o sentido de rotação do motor, o driver também é capaz de controlar a velocidade do motor. Utiliza-se um sinal PWM para regular o nível de rotação do eixo. 

A modulação por largura de pulso (PWM) é uma técnica fundamental que envolve a variação da largura dos pulsos em um sinal elétrico para transmitir informações. Em vez de manter um sinal em níveis constantes, o PWM altera a largura dos pulsos, controlando o tempo em que a chave fica ligada e desligada. Isso permite administrar a quantidade média de energia que chega à carga e, consequentemente, a potência elétrica <a href=“../eletronica-energia/Projeto_do_Subsistema_de_Energia.md#ref-4“> [4]</a>.

Essa técnica é amplamente utilizada em diversos equipamentos eletrônicos de potência, como drivers de LED, inversores de frequência e controle de velocidade de motores. No cotidiano, o PWM é encontrado em carregadores, sistemas fotovoltaicos, servo-motores e carros elétricos, entre outros <a href=“../eletronica-energia/Projeto_do_Subsistema_de_Energia.md#ref-7“> [7]</a>.

O ciclo de trabalho, ou Duty Cycle mostrado na figura, é um parâmetro crucial para controlar um sinal PWM. Ele representa a relação entre a largura do pulso e o período, informando o tempo em que o sinal está em nível alto (ligado) e o tempo em que está em nível baixo (desligado). 

O Duty Cycle é expresso em porcentagem e calculado pela fórmula D = (PW / T) x 100%, onde PW é a largura do pulso e T é o período <a href=“../eletronica-energia/Projeto_do_Subsistema_de_Energia.md#ref-5“> [5]</a>. Deste modo, o sinal 255 da placa é convertido para um sinal PWM de 100%, e o sinal 0 da placa é convertido para um sinal PWM de 0%. Portanto um sinal de 127 da placa será convertido para um sinal PWM de 50%. Consequentemente, para um motor, o sinal 0 seria o motor parado, já o sinal 255 seria a sua rotação máxima. Abaixo é possível ver um exemplo com o sinal PWM sendo aplicado em um LED <a href=“../eletronica-energia/Projeto_do_Subsistema_de_Energia.md#ref-5“> [5]</a>.
</p>



<font size="2"><p style="text-align: center">Figura 13: Representação do comportamento do controle PWM.</p></font>

<p style="text-align:justify;">
Uma das principais vantagens do PWM é a manutenção do sinal digital em todo o percurso, o que minimiza os efeitos de ruído. Além disso, o PWM oferece maior imunidade ao ruído em comparação ao controle analógico, o que torna essa técnica ideal para comunicações. Em sistemas de freios controlados por modulação, por exemplo, o PWM é utilizado para controlar a pressão exercida pelo freio de acordo com a quantidade de tensão ou corrente aplicada <a href=“../eletronica-energia/Projeto_do_Subsistema_de_Energia.md#ref-4“> [4]</a>.
</p>



<font size="2"><p style="text-align: center">Figura 14: Funcionamento do PWM num led.
Fonte <a href=“../eletronica-energia/Projeto_do_Subsistema_de_Energia.md#ref-5“> [5]</a>.</p></font>

### Funcionamento do Driver L298N
<p style="text-align:justify;">
O módulo L298N utiliza as portas In1, In2 e EnA para controlar o motor "A" (lado esquerdo do diagrama de blocos da imagem da figura 11). Os pinos In1 e In2 são responsáveis pelo direcionamento do sentido do motor, e o pino EnA é responsável pela regulação de velocidade do motor "A", portanto o pino de saída da BlackBoard para o pino EnA do módulo deverá permitir um sinal PWM. 

Da mesma maneira que o motor "A", o motor "B" possui dois pinos de direcionamento de sentido, porém ao invés de serem os pinos In1 e In2, são os pinos In3 e In4. O pino que determina a velocidade do motor "B" é o EnB, que também deve permitir um sinal PWM vindo da BlackBoard. É possível observar o diagrama de blocos do funcionamento do chip L298N Figura 15.
</p>

 

<font size="2"><p style="text-align: center">Figura 15: Diagrama de blocos do L298M
Fonte <a href=“../eletronica-energia/Projeto_do_Subsistema_de_Energia.md#ref-7“> [7]</a>.</p></font>

## Módulo Regulador C/LM2596
<p style="text-align:justify;">
O circuito precisa de um módulo que permita trabalhar com duas tensões, uma de 12V para alimentar a Ponte H, e um de 5V para alimentar a placa de árduino, para resolver esta situação foi trabalhado com um fonte de 12V e um módulo regular C/LM2596 (ver figura 16 e 17). O Módulo Regulador de Tensão LM2596 trabalha como um conversor DC DC no modo Step Down, sendo capaz de reduzir uma carga de até 3A com ótima eficiência. 

A tensão de saída pode ser ajustada entre 1,5 a 35v, tendo como entrada 3,2 a 40v. Possui uma velocidade de comutação de 150KHz e pode ser aplicado em circuitos onde a saída de um sensor é superior a 5v, tensão de entrada máxima em um Arduino ou PIC <a href=“../eletronica-energia/Projeto_do_Subsistema_de_Energia.md#ref-8“> [8]</a>.
</p>



<font size="2"><p style="text-align: center">Figura 16: Módulo regular C/LM2596.</p></font>



<font size="2"><p style="text-align: center">Figura 17: Especificação dos componentes do módulo regulador C/LM2596.</p></font>

<p style="text-align:justify;">
Este módulo tem as seguintes carácterísticas:
</p>



<p style="text-align:justify;">
Assim conhecendo todos os componentes, foi montada uma simulação utilizando programa Proteus, a qual é motrada na Figura 18. Já na Figura 19, encontra-se a representação do circuito realizada utilizando o Fritzing que permite gerar o diagrama esquemático do circuito na Figura 20, e o diagrama de barramento na Figura 21.
</p>

 

<font size="2"><p style="text-align: center">Figura 18: Simulação do Proteus do sistema de motores.</p></font>

<p style="text-align:justify;">
A Figura 18 apresenta a simulação realizada no proteus para verificar o funcionamento do motor e um preteste do funcionamento dos motores, seguidamente foi feita a simulação utilizando o Fritzing com o objetivo de criar os diagramas esquemáticos.
</p>

 

<font size="2"><p style="text-align: center">Figura 19: Simulação Arduino do sistema de motores.</p></font>

<p style="text-align:justify;">
Já nas Figuras 20 e 21 se apresentam os diagramas de eletrônica de blocos e de barramento respectivamente.
</p>

 

<font size="2"><p style="text-align: center">Figura 20: Diagrama de blocos completo do circuito com motores de passo.</p></font>

  

<font size="2"><p style="text-align: center">Figura 21: Diagrama de barramentos completo do circuito com motores de passo.</p></font>

## Descrição Matemática do Motor
<p style="text-align:justify;">
Um motor pode ser modelado utilizando um Resistor, um indutor e uma força contra eletromotriz que relaciona o fluxo magnético gerado pelo motor em função do fluxo magnético e do número de espiras que ele tem, sendo assim esta força é modelada pela relação de Faraday como se mostra na equação 1:
</p>



<p style="text-align:justify;">
A equação que representa a tensão pode ser modelada aplicando a LKT, representada como mostra a equação 2 e a Figura 22:
</p>





<font size="2"><p style="text-align: center">Figura 22: Modelo Elétrico do motor DC.</p></font>

<p style="text-align:justify;">
O motor pode ser separado em variáveis elétricas e mecânicas, conforme mostra a figura 4, onde a parte ressaltada na cor preto, indica a parte elétrica e a ressaltada na cor vermelho a parte mecânica como.
</p>



<font size="2"><p style="text-align: center">Figura 23: Modelo elétrico e mecânico do motor DC.</p></font>



<p style="text-align:justify;">
O campo incidente sobre o motor é chamado campo fixo, esse campo fixo pode ser gerado por uma bobina ou imã permanente, supondo que a corrente elétrica de campo constante, descartando efeitos secundários, em uma máquina rotativa a variação do fluxo magnético sobre a bobina é proporcionar a velocidade angular como mostra a equação 3.
</p>



<font size="2"><p style="text-align: center">Figura 24: Representação do campo magnético no motor.</p></font>



<p style="text-align:justify;">
Assim a força contra eletromotriz é proporcional ao fluxo, desta forma pode ser representada como mostra a equação 4:
</p>



<p style="text-align:justify;">
Como a força exercida nos condutores é proporcional à corrente elétrica que passa pelo condutor, o torque do motor é proporcional à corrente, e se iguala quando se utiliza uma constante de torque \( Kt \), como mostra a equação 5.
</p>



<p style="text-align:justify;">
Assim a potência é produto do torque pela velocidade angular desenvolvida pelo motor, desta forma:
</p>



<p style="text-align:justify;">
Outro parâmetro considerado é o torque inercial, o qual tem como trabalho suprimir todas as perdas e ser suficiente para acelerar o motor até um ponto de inércia, ele pode ser representado como a equação 7:
</p>





<p style="text-align:justify;">
O torque total de atrito do motor ou de arrasto, depende da velocidade angular do motor, ele é dependente do coeficiente de arrasto ou atrito viscoso do motor, assim o torque total do motor é:
</p>



<p style="text-align:justify;">
Substituindo o torque total, encontra-se a relação de corrente como mostra a equação 9:
</p>



<p style="text-align:justify;">
Substituído a corrente na equação geral do motor, encontramos a representação da velocidade angular em função da velocidade de entrada do motor, como mostra equação 10:
</p>



<p style="text-align:justify;">
Realizando procedimentos matemáticos, e derivando o termo do indutor e reagrupando termos é obtida a equação diferencial não homogênea mostrada na equação 11:
</p>



<p style="text-align:justify;">
A velocidade máxima pode ser calculada como:
</p>



<p style="text-align:justify;">
Aplicando a transformada de Laplace para a EDO com condições iniciais nulas, encontra-se a função de transferência geral descrita na equação:
</p>



### Cálculo dos Parâmetros do Motor
<p style="text-align:justify;">
Para calcular os parâmetros do motor, é necessário conhecer as características dele publicadas pelo fabricante, considerando que os motores de passo tem o código NEMA 17 4.2Kgf 1.7A (Stepper Motor 17HS4401).
</p>
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

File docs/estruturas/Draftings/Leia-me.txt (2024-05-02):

Procedimentos para criaar o drafiting

1.	Copiar o modelo de cabeçalho do drafitind "Caixa_estrutura_tampa" no SheetBackground;
1.1.	Lembrar de sempre colocar o nome de quem fez cada coisa;

2. 	Salvar com o nome composto pelo subsistema, depois nome da peça separadas com hifem. ex: estrutura_aluminio_estrudado;

3. 	Salvar uma cópia em .CATDrawing e outra em .PDF.

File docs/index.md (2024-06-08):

<div>
  <center>
  
  <h3 style="color: #000000; text-align: center">

<p style="text-align:justify;">No mundo contemporâneo, a integração entre dispositivos inteligentes e processos automatizados tem revolucionado diversos setores, impulsionando a eficiência e a produtividade. Nesse contexto, surge o projeto ScanPoint como uma resposta inovadora para simplificar e aprimorar o processo de digitalização 3D e reprodução tridimensional de objetos físicos.</p>
<p style="text-align:justify;">O ScanPoint é composto por uma mesa escaner e um aplicativo desktop. A mesa scaner foi desenvolvida com um Arduino e sensores infravermelhos, capazes de realizar leituras de objetos em tempo real. Esses dados são enviados para o aplicativo desktop, que permite o acompanhamento do processamento dos pontos capturados e serve de interface para a disponibilização do arquivo em formato STLe seu download. O processo de modelagem envolve a captura e processamento de dados para criar um modelo virtual o mais preciso possível. Esses modelos podem ser salvos e exibidos para o usuário, permitindo que reinicie o processo caso não esteja satisfeito antes de realizar o download.</p>
<p style="text-align:justify;">Essa solução pode ser aplicada em diversos setores, como manufatura, engenharia, design de produtos e educação. A aceleração da produção é uma das principais vantagens, permitindo que modelos 3D sejam desenvolvidos rapidamente a partir de leituras instantâneas, aumentando a precisão, reduzindo custos e o tempo de produção. Por exemplo, na engenharia, o sistema pode ser utilizado para criar protótipos e peças com maior rapidez e precisão.</p>
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

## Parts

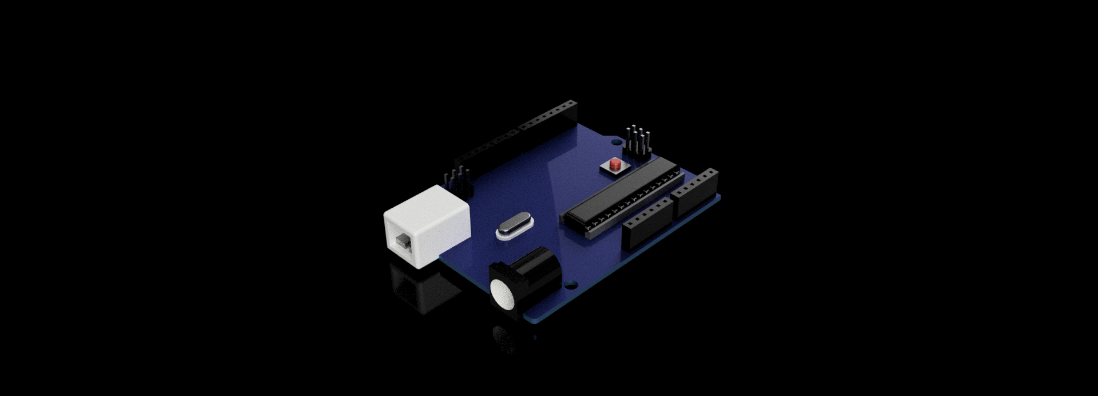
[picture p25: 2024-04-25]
docs/estruturas/CAD/Estrutura_CATIA/Componentes avulsos/arduino-uno/ARDUINO v5.png

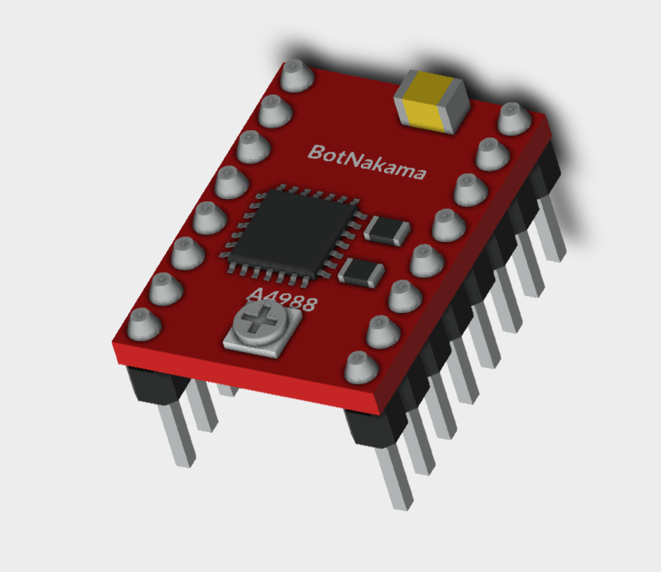
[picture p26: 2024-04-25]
docs/estruturas/CAD/Estrutura_CATIA/Componentes avulsos/a4988-8.snapshot.1/A4988.png

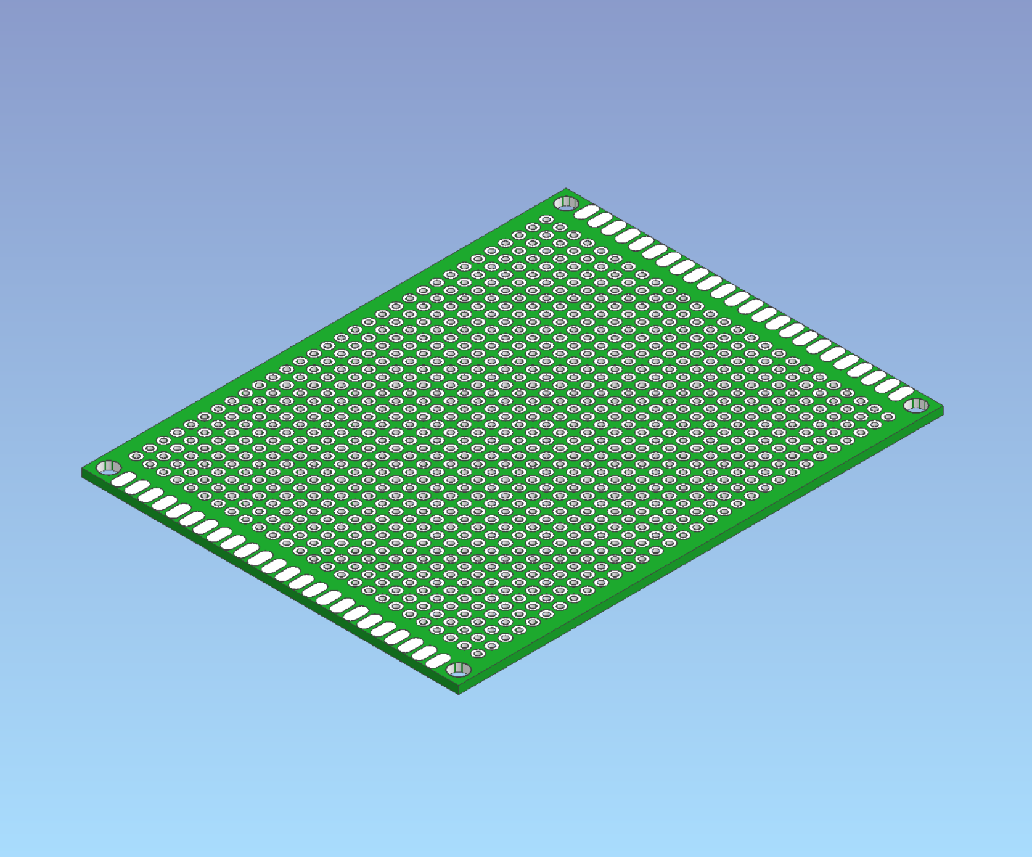
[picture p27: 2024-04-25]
docs/estruturas/CAD/Estrutura_CATIA/Componentes avulsos/universal_board_70x90mm_2-54mm_hole31x26-1.snapshot.2/Universal_board_70x90mm_31x26.png

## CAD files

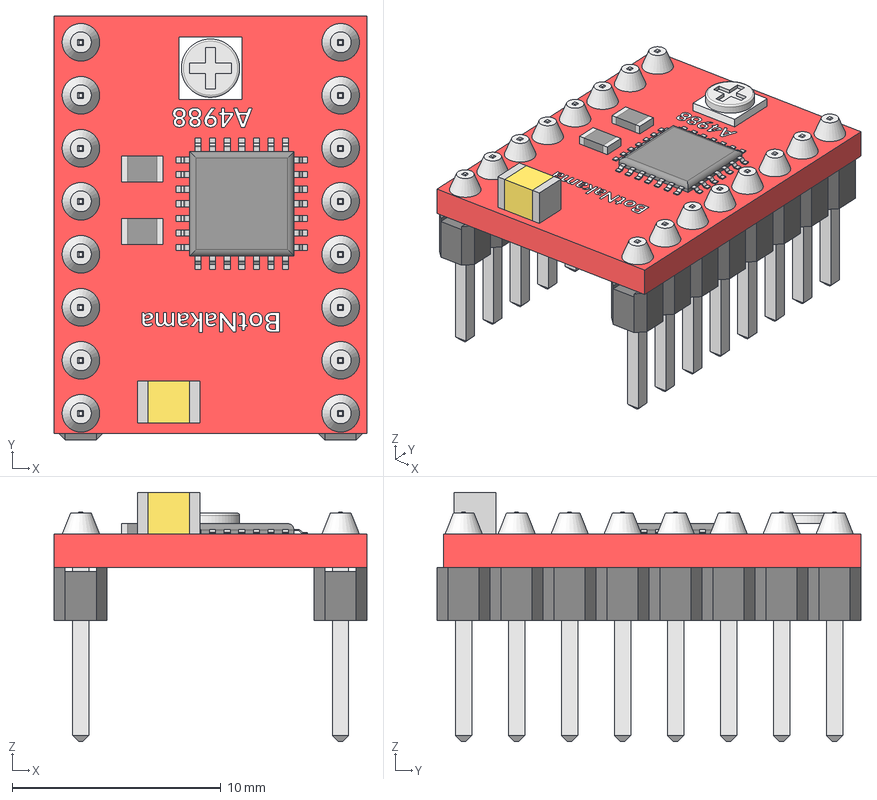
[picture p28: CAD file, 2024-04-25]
docs/estruturas/CAD/Estrutura_CATIA/Componentes avulsos/a4988-8.snapshot.1/A4988.stp
15.0 x 20.3 x 11.9 mm
Integrado
Cubo001
BotNakama
A4988_1

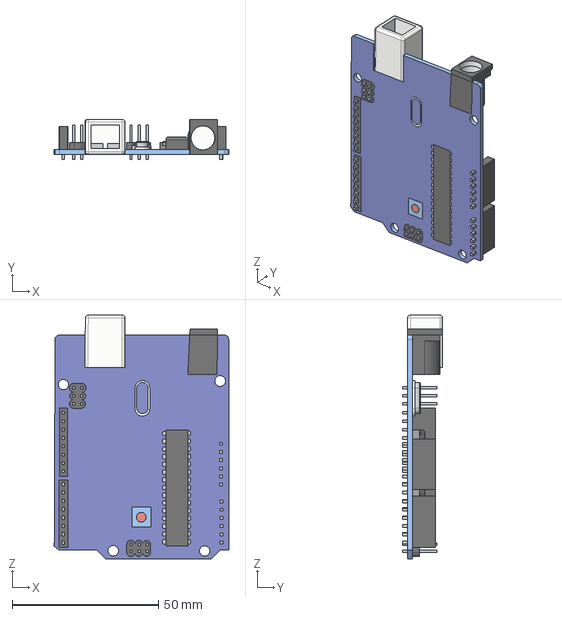
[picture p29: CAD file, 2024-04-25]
docs/estruturas/CAD/Estrutura_CATIA/Componentes avulsos/arduino-uno/ARDUINO v5.step
59.7 x 13.8 x 83.4 mm

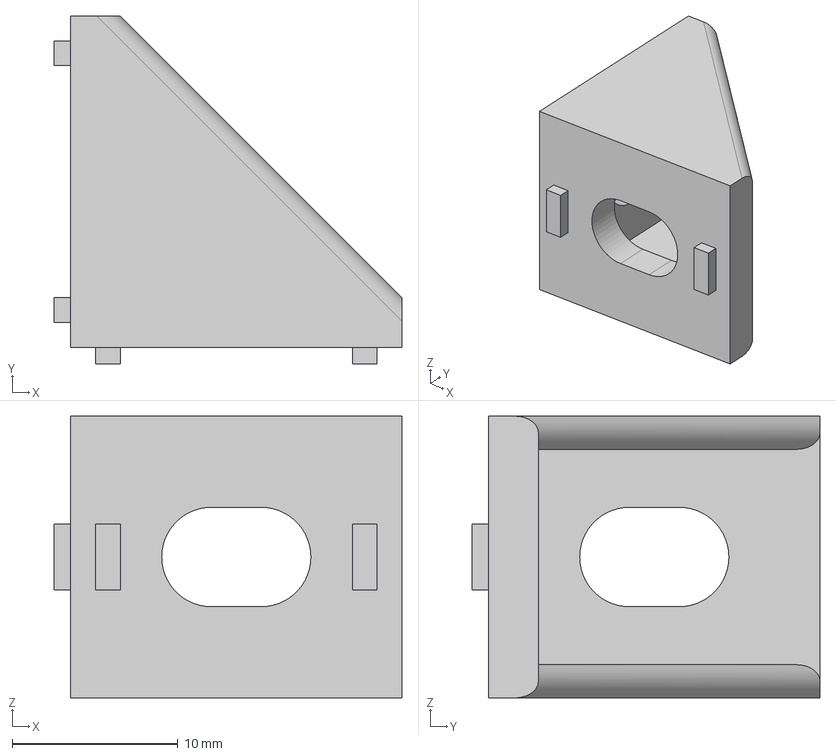
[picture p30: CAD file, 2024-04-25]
docs/estruturas/CAD/Estrutura_CATIA/Componentes avulsos/cantoneira-20x20x17-p-v-slot-e-t-slot-1.snapshot.2/Cantoneira 20x20x17 v6.step
21.0 x 21.0 x 17.0 mm

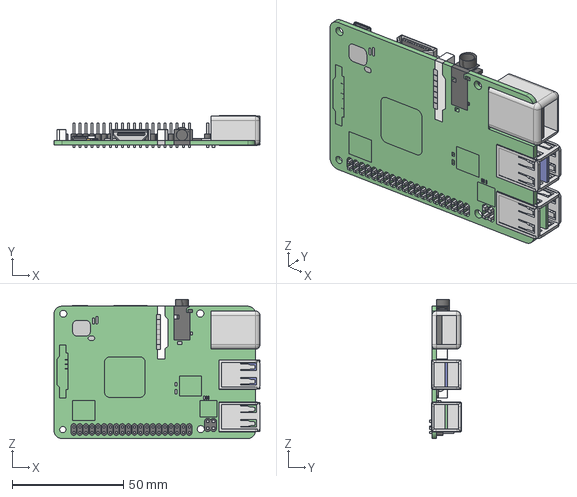
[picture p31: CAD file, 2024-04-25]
docs/estruturas/CAD/Estrutura_CATIA/Componentes avulsos/raspberry-pi-3-4.snapshot.1/RASBERRY PI v6 v4.step
92.7 x 14.2 x 62.6 mm

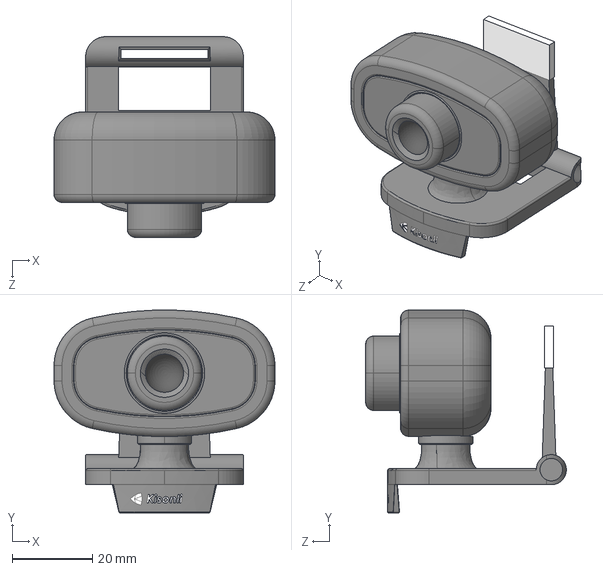
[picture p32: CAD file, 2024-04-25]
docs/estruturas/CAD/Estrutura_CATIA/Componentes avulsos/webcam-28.snapshot.4/Webcam.STEP
55.0 x 50.5 x 50.0 mm

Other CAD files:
docs/assets/eletronica-energia/Diagrama_unifilar.dwg
docs/estruturas/CAD/Estrutura_CATIA/Bateria/Bateria.CATPart
docs/estruturas/CAD/Estrutura_CATIA/Caixa_Eletronica/Base.CATPart
docs/estruturas/CAD/Estrutura_CATIA/Caixa_Eletronica/Caixa_montada.CATProduct
docs/estruturas/CAD/Estrutura_CATIA/Caixa_Eletronica/Lateral_Maior.CATPart
docs/estruturas/CAD/Estrutura_CATIA/Caixa_Eletronica/Lateral_Menor.CATPart
docs/estruturas/CAD/Estrutura_CATIA/Caixa_Eletronica/Motor.CATPart
docs/estruturas/CAD/Estrutura_CATIA/Caixa_Eletronica/Motor_de_passo.CATPart
docs/estruturas/CAD/Estrutura_CATIA/Caixa_Eletronica/Topo.CATPart
docs/estruturas/CAD/Estrutura_CATIA/Caixa_Eletronica/suporte do motor_ATUALIZADO.CATPart
docs/estruturas/CAD/Estrutura_CATIA/Caixa_Eletronica/suporte placas_ATUALIZADO.CATPart
docs/estruturas/CAD/Estrutura_CATIA/Componentes avulsos/a4988-8.snapshot.1/A4988.CATProduct
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

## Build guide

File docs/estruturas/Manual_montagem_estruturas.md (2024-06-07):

# Manual de Montagem

## Etapa 1

<p style="text-align: justify;">
Para a montagem da estrutura, é recomendável que se inicie pela base de alumínio. Tal componente será usado de gabarito para posicionamento da caixa de madeira e junção geral da estrutura. A base de alumínio leva apenas:
</p>

* 8 perfis de alumínio,
* 8 cantoneiras de alumínio e 
* 16 parafusos m4 com porcas martelo.

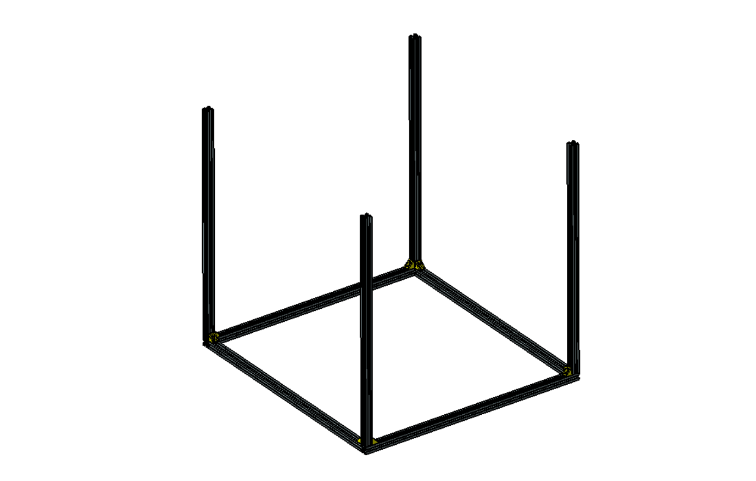
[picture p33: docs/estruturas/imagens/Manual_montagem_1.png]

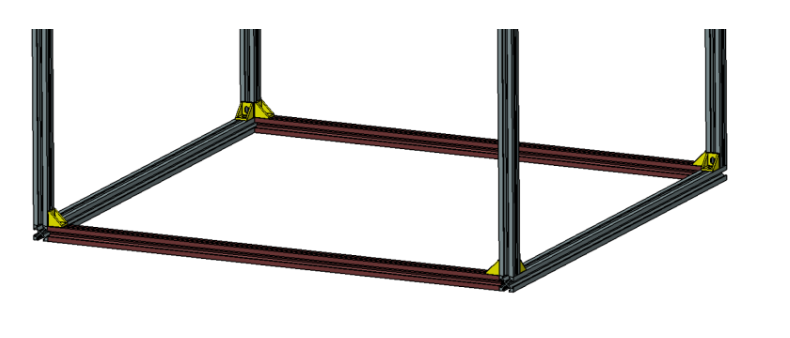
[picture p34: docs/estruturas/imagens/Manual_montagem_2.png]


<p style="text-align: justify;">
Note no detalhamento que os perfis destacados em marrom devem ser posicionados internamente, já os demais são posicionados externamente na estrutura.
</p>

## Etapa 2

<p style="text-align: justify;">
 Após a montagem, deve-se escolher um dos dois perfis externos da base e desmontar para a inclusão da base de madeira. A base de madeira é a peça de maiores dimensões (662mm x 622mm) e deve correr entre os vincos dos perfis de forma que fique fixa em todas as direções. As figuras abaixo representa tal processo:
</p>

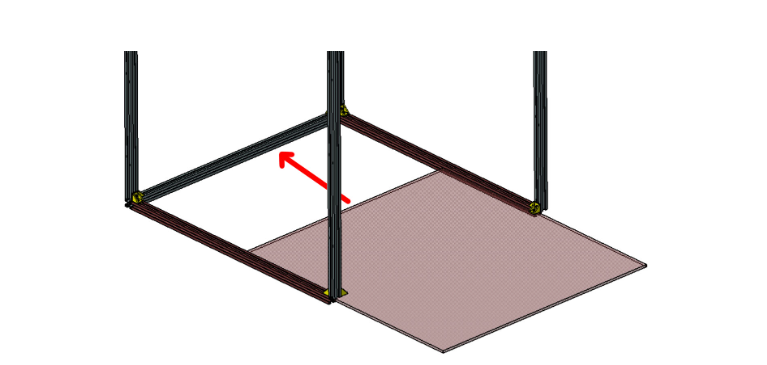
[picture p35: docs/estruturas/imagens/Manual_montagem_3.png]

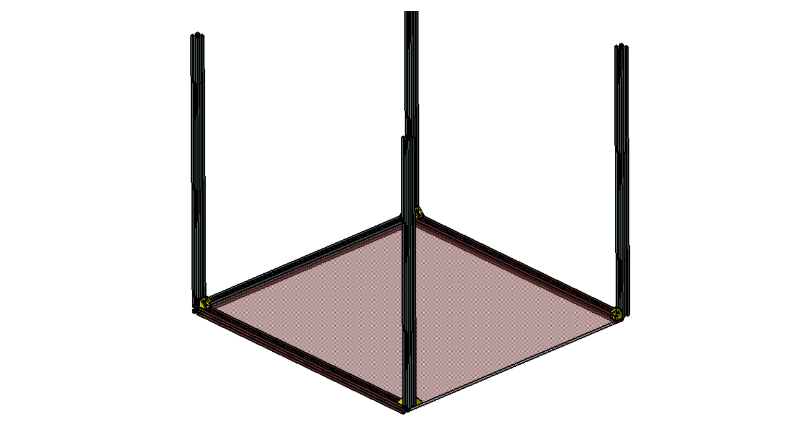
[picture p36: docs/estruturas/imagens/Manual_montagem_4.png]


<p style="text-align: justify;">
 Por fim, o perfil de alumínio removido é fixado novamente em sua posição de origem, impedindo o movimento da placa de madeira da base:
</p>

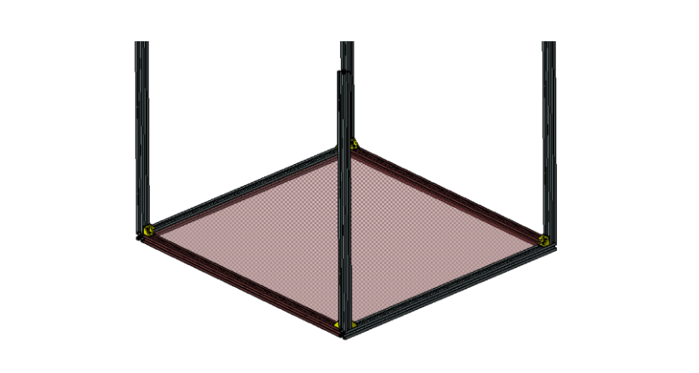
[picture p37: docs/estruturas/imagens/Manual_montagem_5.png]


## Etapa 3

<p style="text-align: justify;">
 A terceira etapa do processo de montagem é o subsistema da caixa da eletrônica. A caixa da eletrônica é composta de 5 peças principais sendo elas: 
</p>

* 2 Paredes laterais menores (598mm x 140mm)
* 2 Paredes laterais maiores (650mm x 140mm)
* c1 Base (662mm x 622mm)

Para a montagem desse subsistema serão necessárias: 

* cianoacrilato (mais conhecido como adesivo instantâneo ou CA) 
* ou cola de madeira.

<p style="text-align: justify;">
 Note que a base (662mm x 622mm) já está posicionada entre os perfis. Assim, inicia-se o processo de montagem colando as paredes laterais maiores paralelas à maior medida da base. As paredes laterais devem ficar rentes as dobradiças e as paredes menores devem ir internamente às maiores, conforme mostra a figura:
</p>

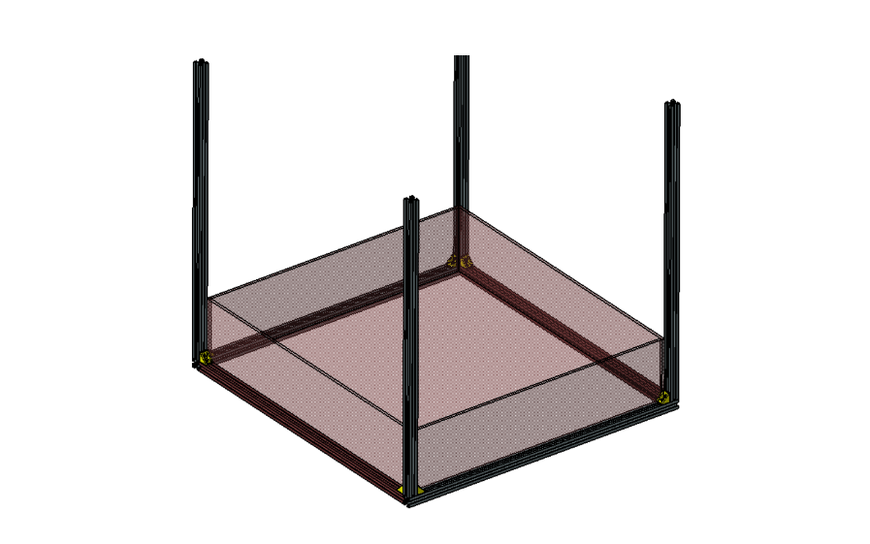
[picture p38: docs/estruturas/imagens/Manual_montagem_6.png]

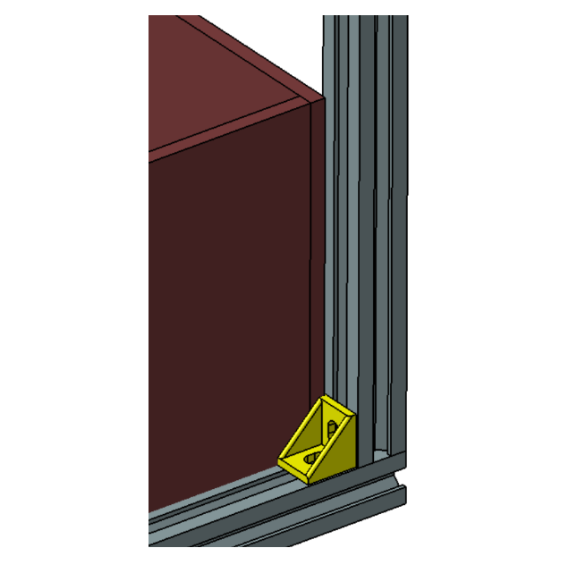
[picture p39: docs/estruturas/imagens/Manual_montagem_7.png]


<p style="text-align: justify;">
Podemos observar no detalhamento acima que a parede lateral menor deve ir internamente à parede lateral maior.
</p>

## Etapa 4

<p style="text-align: justify;">
Deve-se, agora, posicionar as duas tampas (610mm x 325mm), que não devem ser coladas, a fim de permitir alguma eventual manutenção interna dos componentes. Para tanto, utilizaremos:
</p>

* 4 dobradiças;
* 2 fechos de caixa de madeira;
* 16 parafusos M4 com porcas. 

<p style="text-align: justify;">
Iniciaremos o processo de montagem unindo ambas as tampas por meio de duas dobradiças, conforme a imagem:
</p>

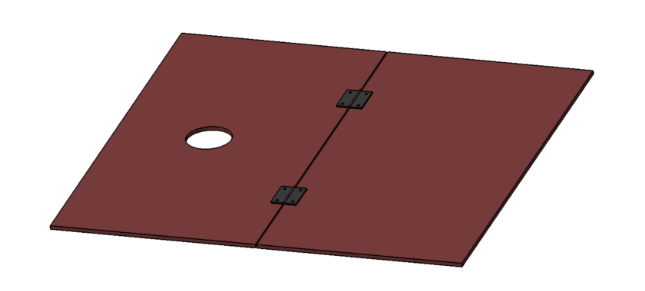
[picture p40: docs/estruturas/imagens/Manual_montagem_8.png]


<p style="text-align: justify;">
A fixação das dobradiças será realizada com os parafusos e porcas M4.
</p>

<p style="text-align: justify;">
Para seguir essa etapa, devemos agora posicionar mais duas dobradiças na menor lateral da placa não furada:
</p>

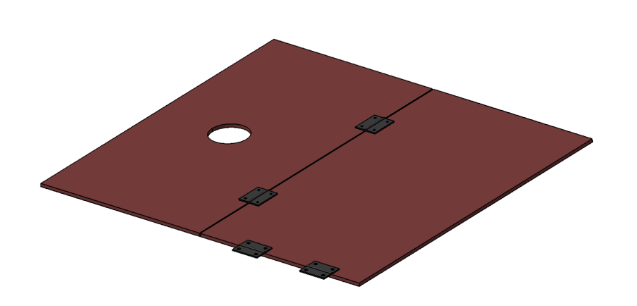
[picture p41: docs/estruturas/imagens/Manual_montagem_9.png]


<p style="text-align: justify;">
Por fim, posicionamos a peça fêmea dos fechos nas laterais opostas às dobradiças: 
</p>

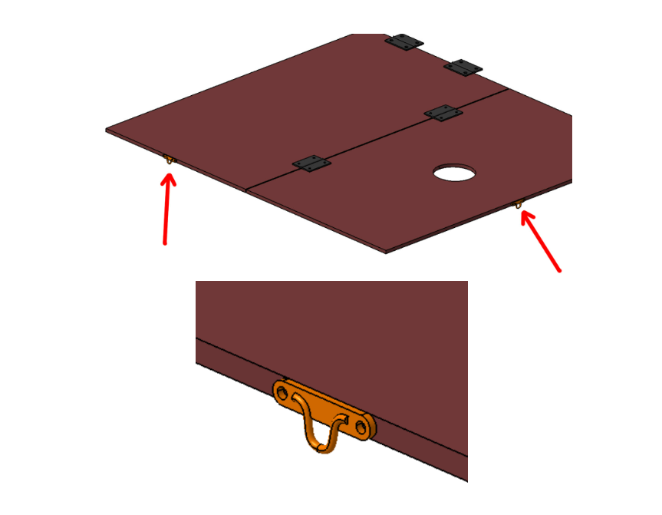
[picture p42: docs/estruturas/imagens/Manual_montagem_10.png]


<p style="text-align: justify;">
Um componente essencial dessa montagem é o motor de passo e seu suporte, que deve ser fixado na parte debaixo da tampa, centralizado com o furo da placa e parafusado utilizando :
</p>

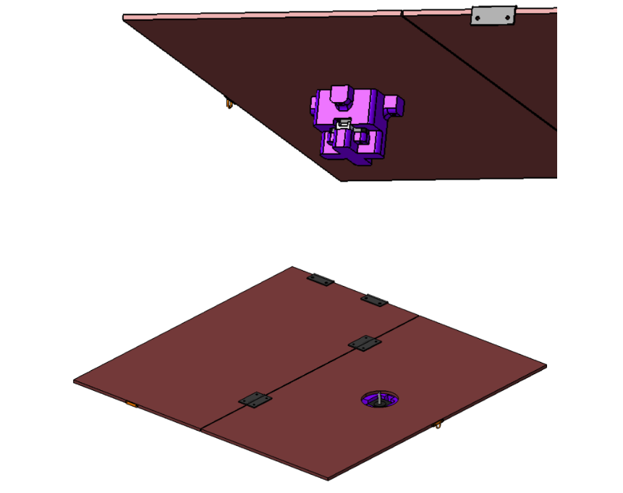
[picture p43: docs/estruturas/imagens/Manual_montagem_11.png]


<p style="text-align: justify;">
Ainda na parte inferior da tampa, porém agora na metade não furada, devemos posicionar centralizada a peça de suporte das guias, também impressa, representada de azul na figura, o motor de passe deve ser parafusado acima com parafusos M3, respeitando a furação já existente:
</p>

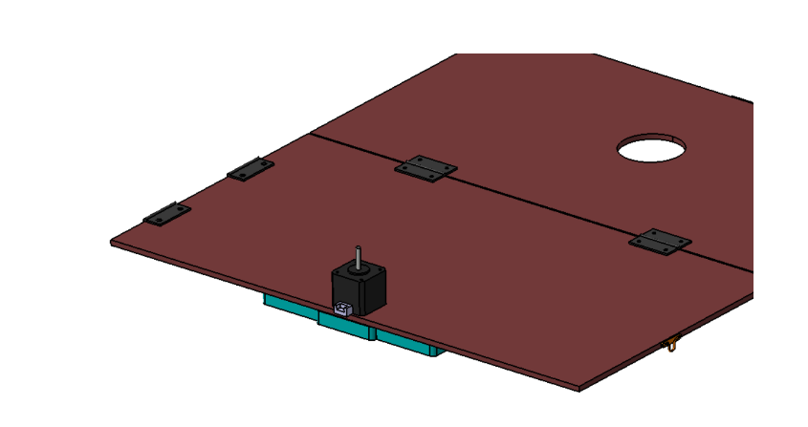
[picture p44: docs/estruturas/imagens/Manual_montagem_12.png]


<p style="text-align: justify;">
Finalmente a tampa deve ser fixada na caixa da eletrônica, através de 4 parafusos M4 para as dobradiças e do conjunto macho do fecho com seus parafusos:
</p>

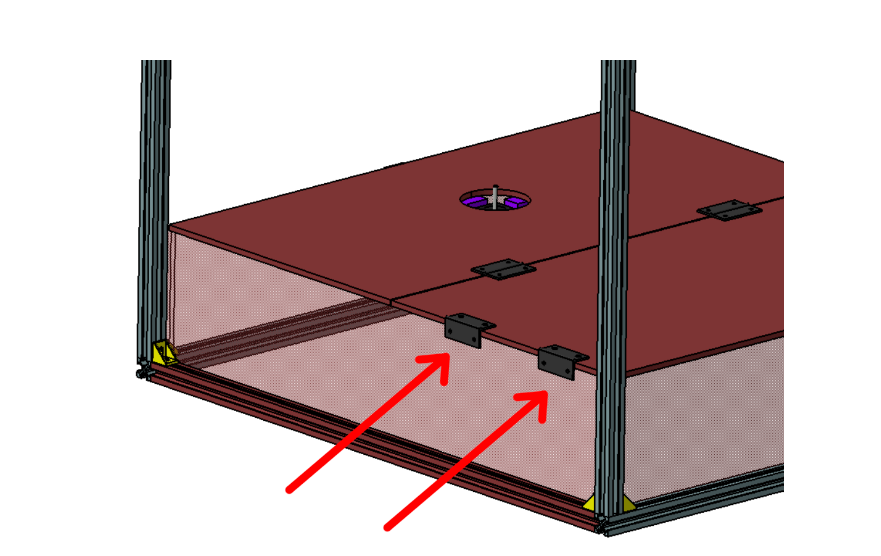
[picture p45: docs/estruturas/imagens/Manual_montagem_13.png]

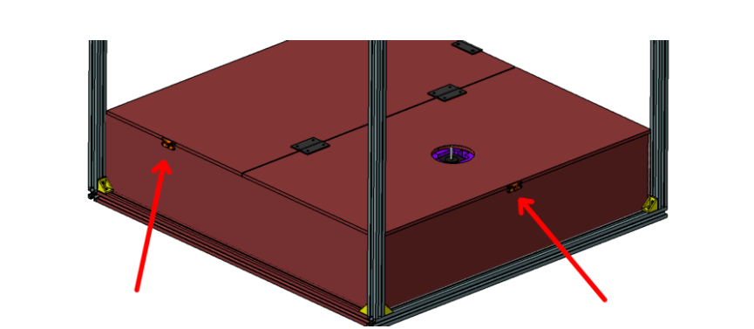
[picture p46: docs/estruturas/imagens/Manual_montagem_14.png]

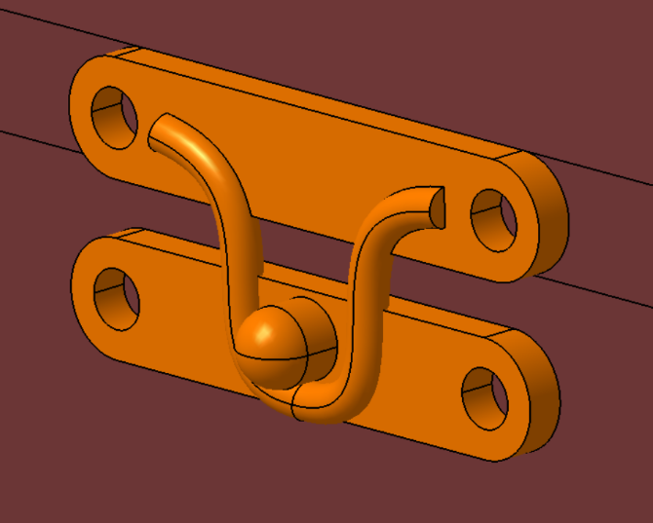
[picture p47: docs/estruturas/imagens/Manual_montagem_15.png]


## Etapa 5

<p style="text-align: justify;">
Partindo agora para a fixação final da tampa na estrutura de alumínio, de cima para baixo, desliza-se as peças impressas em 3D, da maneira como está descrita na imagem e atentando-se para o posicionamento individual de cada uma, após isso realiza-se a fixação com parafusos M4, porcas e arruelas, partindo do topo da peça impressa até a parede da tampa, repetindo para os 4 cantos da estrutura. Atente-se para posicionar uma porca martelo em cada um dos slots da peça impressa, como destacado em verde na primeira figura:
</p>

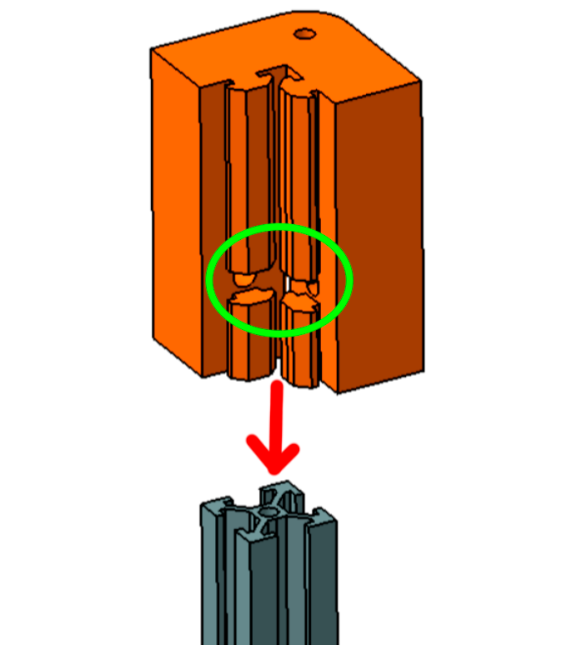
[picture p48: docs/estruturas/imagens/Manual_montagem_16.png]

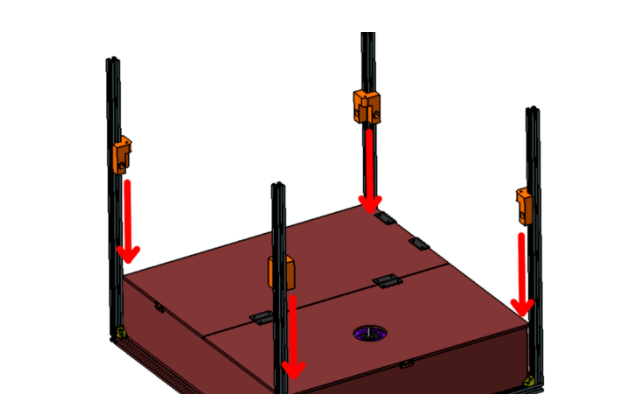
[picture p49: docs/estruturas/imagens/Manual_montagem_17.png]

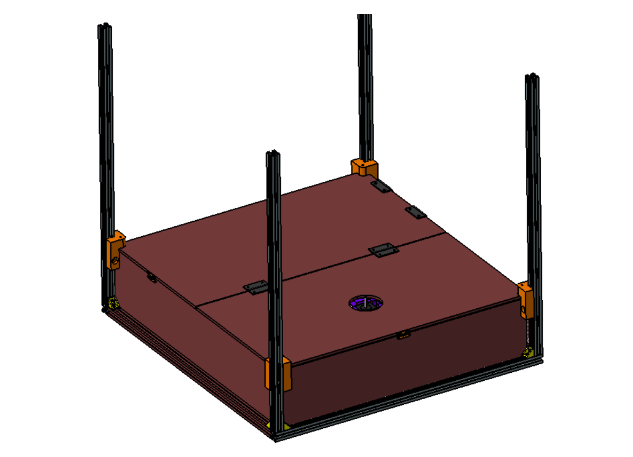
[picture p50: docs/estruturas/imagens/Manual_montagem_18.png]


<p style="text-align: justify;">
Por fim, utilizando parafusos M4 e arruelas, deve-se parafusar as peças impressas diretamente nos perfis de alumínio, com auxílio das porcas-martelo, já posicionadas anteriormente.
</p>

## Etapa 6

<p style="text-align: justify;">
Respeitando a furação da peça azul, deve-se agora posicionar os encaixes de alumínio das guias, as guias e, com um acoplador de 8mm, o fuso no motor do eixo:
</p>

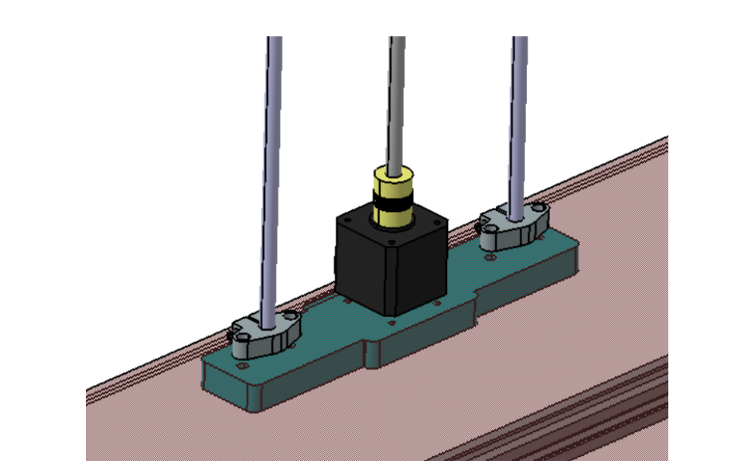
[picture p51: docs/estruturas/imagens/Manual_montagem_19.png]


<p style="text-align: justify;">
Após, desliza-se o suporte do sensor com os rolamentos lineares atráves da guia, rotacionando o fuso na castanha para que o sistema desça uniformemente:
</p>

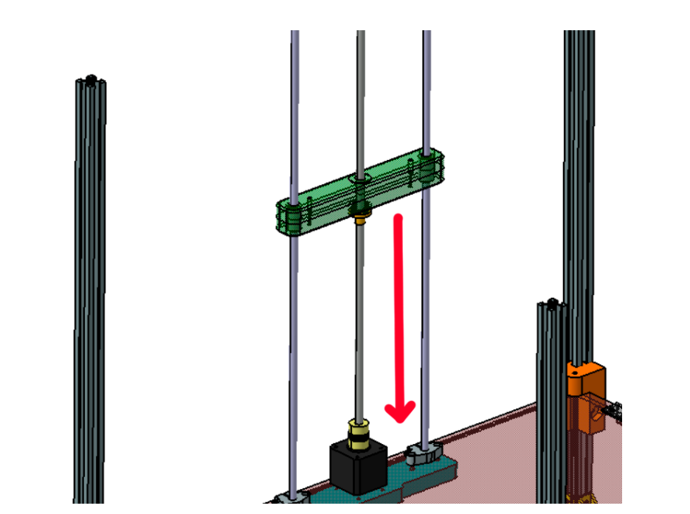
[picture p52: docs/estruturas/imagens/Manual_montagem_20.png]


<p style="text-align: justify;">
Finalizando o conjunto do trilho, adiciona-se a peça superior impressa ao conjunto, com os apoios de alumínio e o rolamento posicionado, essa peça é deslizada em um perfil de alumínio que é fixado aos perfis verticais, conforme a representação:
</p>

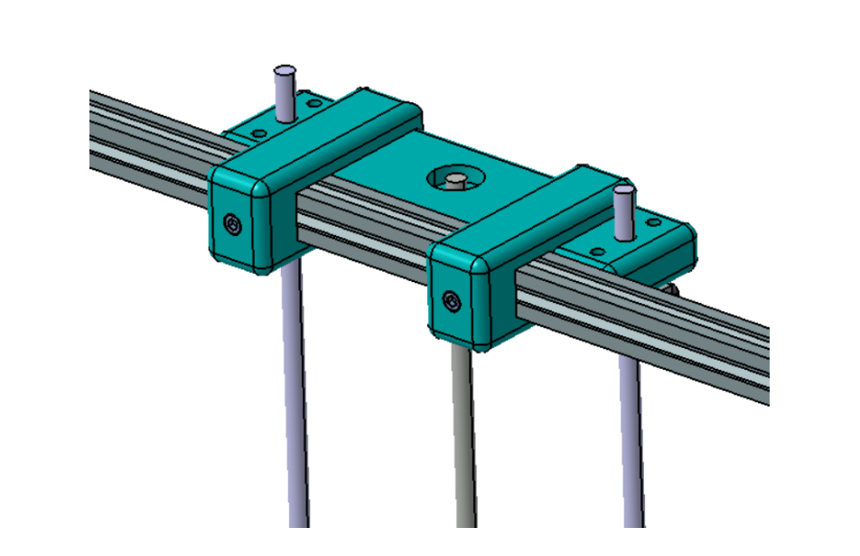
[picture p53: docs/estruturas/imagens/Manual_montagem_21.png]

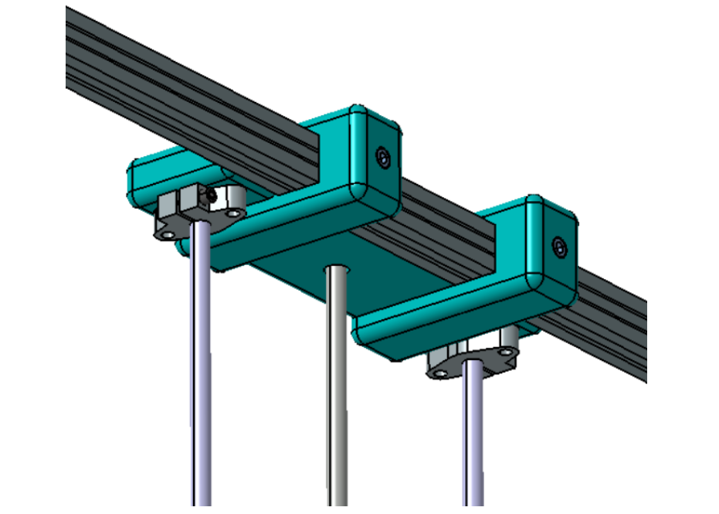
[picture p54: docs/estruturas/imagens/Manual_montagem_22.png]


## Etapa 7

<p style="text-align: justify;">
Finalizando a estrutura, posicionamos os perfis de alumínio restantes, juntamente com as cantoneiras e o prato de acrílico, com o acoplador de impressão 3D e o apoio do prato:
</p>

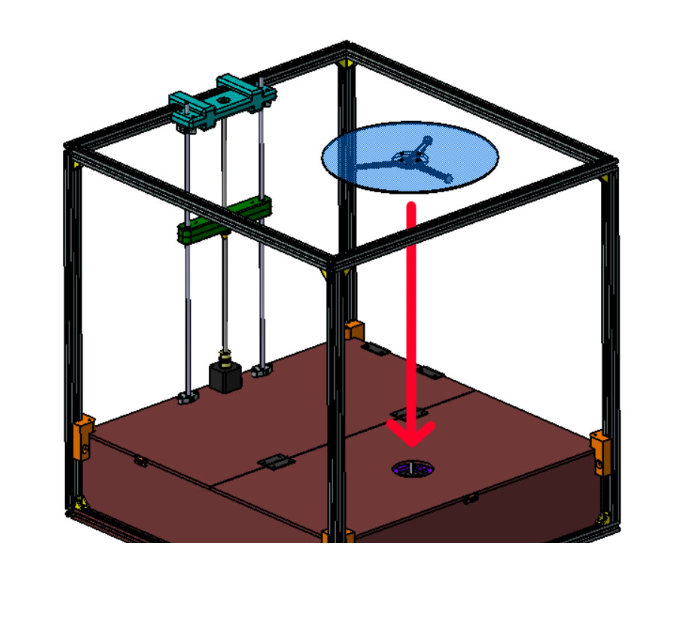
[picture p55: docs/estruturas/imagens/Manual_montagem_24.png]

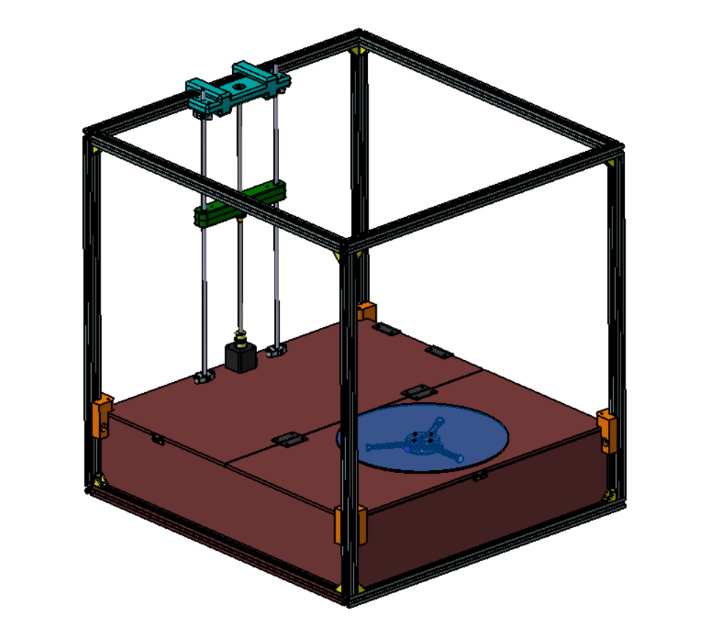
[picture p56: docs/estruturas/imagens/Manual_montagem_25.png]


## Versionamento
| Versão | Data | Modificação | Autor |
|--|--|--|--|
| 1.0 | 07/06/2024 | Entrega | Cássio Filho |

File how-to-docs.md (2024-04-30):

# Como Rodar os documentos

## Requisitos
O único requisito é o [Python 3](https://www.python.org/downloads/) e um terminal ou linha de comando para rodar os comandos de instalação. Ex: Gitbash, CMD, powershell, etc.

**OBS:** Precisaremos do [PIP](https://pip.pypa.io/en/stable/installation/) que é um gerenciador de pacotes do Python normalmente ele já vem instalado.

## Clonando o repositório

O repositório pode ser baixado como um arquivo compatado ou clonado usando git

Para baixar o repositório usando git é sõ executar essa linha de comando

```bash
 $ git clone https://gitlab.com/lappis-unb/fga-pi2/semestre-2024-1/grupo-08/scanpoint.git
```

Para fazer dowload do repositório é clicar em clone depois no formato desejado e depois extrair

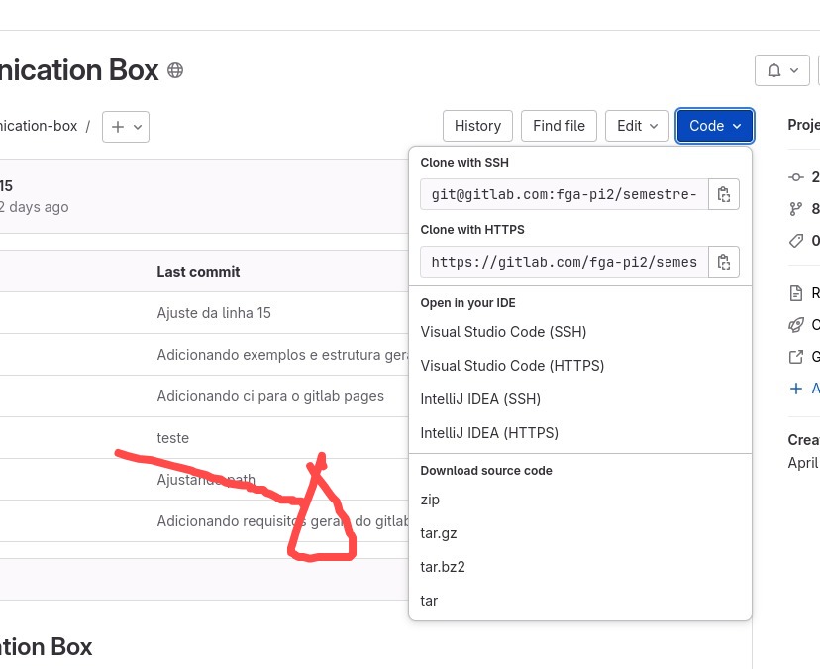
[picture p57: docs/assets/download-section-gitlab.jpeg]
Imagem do local do download


## Intalando e rodando

Depois de baixado entre na pasta do repositório e execute os seguintes comandos

```bash
# Cria um ambiente virtual
$ python3 -m venv venv

# Entra no ambiente virtual
$ source venv/bin/activate

# Instala as dependencias
$ pip install -r requirements.txt

# Rodando os docs

$ mkdocs serve

```
 Depois do ultimo commando os documentos irão estar disponíveis no http://localhost:8000

**OBS:** Para sair do ambiente virtual do python basta digitar
```bash

$ deactivate 

```

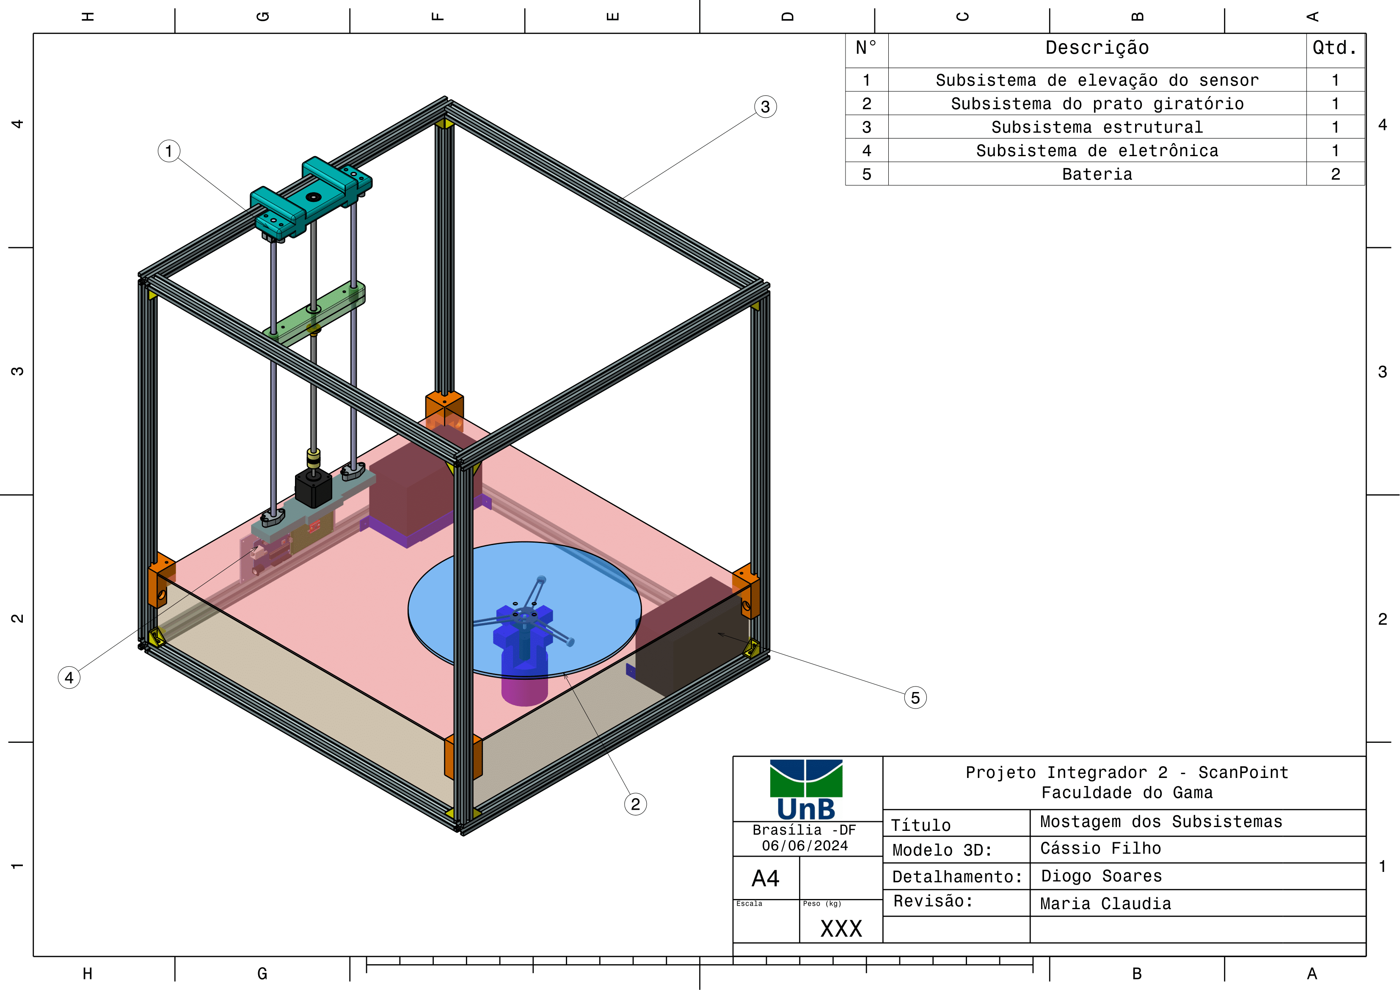
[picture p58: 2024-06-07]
docs/estruturas/imagens/DTs/Montagem-1.png

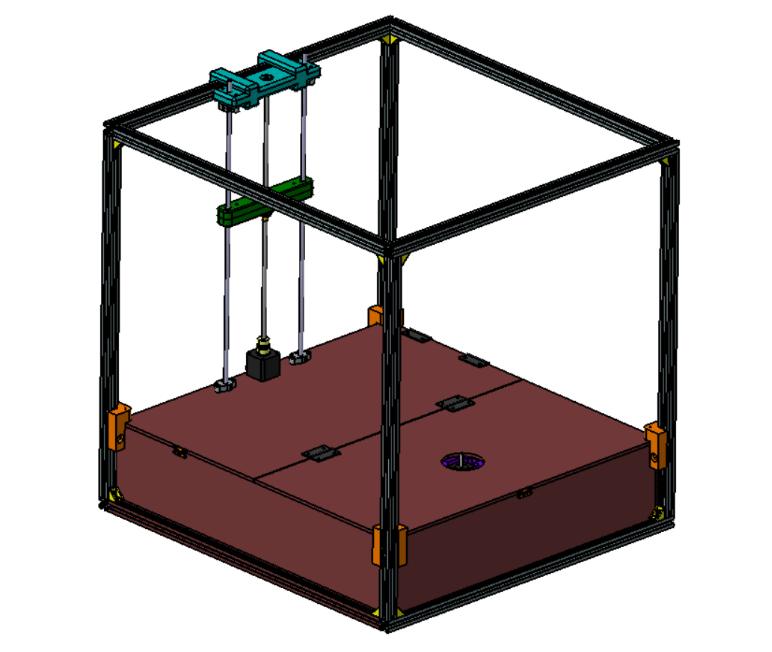
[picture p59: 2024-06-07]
docs/estruturas/imagens/Manual_montagem_23.png

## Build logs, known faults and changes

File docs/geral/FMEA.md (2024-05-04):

# Levantamento de riscos

<p style="text-align:justify;">
O FMEA, ou Análise de Modo e Efeitos de Falha, é uma metodologia usada para identificar e avaliar potenciais falhas em processos, produtos ou sistemas, visando prevenir problemas antes que eles ocorram. Essa técnica é amplamente aplicada em diversos setores, como engenharia, manufatura, saúde e tecnologia, para garantir a qualidade, confiabilidade e segurança dos produtos e processos. Essa metodologia foi escolhida por conta da sua completude de cobertura de análise de riscos, fazendo análise tanto dos módulos de falha quanto das soluções para evitá-las ou corrigi-las, mitigando seus efeitos. </p>

<p style="text-align:justify;">
A análise FMEA envolve uma abordagem sistemática, onde uma equipe multidisciplinar identifica e classifica as possíveis falhas (modo de falha), analisando suas causas e efeitos (efeito da falha), e estimando a gravidade, frequência de ocorrência e detectabilidade de cada falha. Essa análise resulta em uma pontuação de Número de Priorização de Risco (NPR), que permite aos membros priorizar as falhas mais críticas para implementar medidas preventivas ou corretivas.
</p>

<p style="text-align:justify;">
Além disso, o FMEA é uma ferramenta dinâmica, que pode ser revisada e atualizada ao longo do ciclo de vida dos produtos ou processos, garantindo a contínua melhoria e inovação.
Para o projeto atual, foi feito o seguinte FMEA, conforme tabela abaixo: </p>

| No. | Processo | Modo de Falha | Causa da Falha | Efeito da Falha Local | Efeito da Falha Global | Severidade | Ocorrência | Detecção | Número de Priorização de Risco (NPR) | Plano de Ação | Responsável | Prevenção |
| --- | --- | --- | --- | --- | --- | --- | --- | --- | --- | --- | --- | --- |
| 1 | Gestão da Equipe | Indisposição de um membro | Problemas pessoais/saúde | Sobrecarregar outros membros | Atraso nas atividades | 3 | 4 | 1 | 12 | Redistribuição das atividades entre membros competentes | Gerência | Comunicação prévia nas reuniões e/ou grupo de conversa |
| 2 | Montagem do sistema eletrônico | Funcionamento inadequado das baterias | | Não fornecimento de energia suficiente aos equipamentos | Não entrega do projeto por mau funcionamento | 5 | 1 | 1 | 5 | Troca da bateria por uma reserva | Energia | Testes com as baterias |
| 3 | Montagem do sistema eletrônico | Funcionamento inadequado do motor | Falta de alimentação/motor quebrado | Rotação inadequada da mesa durante a leitura da peça | Não entrega do projeto por mau funcionamento | 5 | 1 | 1 | 5 | Troca do motor por um motor reserva | Eletrônica | Testes com o motor |
| 4 | Montagem do sistema eletrônico | Esgotamento da bateria | Mal dimensionamento do tempo de uso | Não fornecimento de energia para os equipamentos | Não entrega do projeto por mau funcionamento | 5 | 2 | 1 | 10 | Troca da bateria por uma reserva | Energia | Dimensionar as baterias de acordo com o tempo de funcionamento do projeto e verificar se o tempo é suficiente para a apresentação |
| 5 | Impressão das peças em 3D | Falta de filamento 3D | Mau cálculo da quantidade de material para a impressão | Estrutura incompleta/Mais tempo para fabricação com outros processos | Atraso na entrega do projeto | 3 | 2 | 1 | 6 | Uso de outros materiais e processo de fabricação para fazer a estrutura | Estrutura | Imprimir com antecedência e revisar o cálculo de quantidade de filamento |
| 6 | Impressão das peças em 3D | Falha na impressão | Falta de energia elétrica/problema com a impressora | Estrutura incompleta/Mais tempo para fabricação com outros processos | Atraso na entrega do projeto | 3 | 2 | 1 | 6 | Uso de outros materiais e processo de fabricação para fazer a estrutura | Estrutura | Imprimir com antecedência e deixar um membro responsável vistoriando a impressão |
| 7 | Fabricação e Montagem | Falta de técnicos/Laboratório fechado | Greve dos professores e técnicos | Impossibilidade de fazer a fabricação e montagem | Atraso ou não entrega do projeto | 5 | 2 | 1 | 10 | Encontrar outro local que se possa fazer a fabricação e montagem | Estrutura | Fazer a fabricação e montagem com antecedência |
| 8 | Desenvolvimento de software | Funcionalidades não entregues | Má gestão de tempo da equipe | Atraso no progresso de desenvolvimento | Não entrega do projeto por mau funcionamento | 3 | 3 | 1 | 9 | Redistribuição das atividades entre membros competentes | Gerência | Acompanhamento das atividades e prazos selecionados |
| 9 | Desenvolvimento de software | Drivers incompatíveis | Softwares não compatíveis na mesma plataforma | Impossibilidade de fazer o desenvolvimento | Atraso na entrega do projeto | 3 | 2 | 2 | 12 | Encontrar novos drivers que consigam trabalhar juntos | Software | Comunicação prévia nas reuniões e/ou grupo de conversa |
| 10  | Desenvolvimento de software | Bugs incorrigíveis | Plataforma ou bibliotecas com erros incorrigíveis | Atraso no progresso de desenvolvimento | Atraso e/ou não entrega do projeto | 3 | 1 | 1 | 3 | Encontrar formas de contornar os erros, seja por código ou substituição de bibliotecas | Software | Testes de build da aplicação |
| 11  | Integração do software com o sistema | Falhas de comunicação dos módulos de software e eletrônica | Conexões ou protocolos | Atraso na Montagem do produto | Atraso e/ou não entrega do projeto | 5 | 1 | 4 | 20 | Fazer uma reunião com os software e de eletrônica para sanar as dificuldades | Software e eletrônica | Micro testes de integração |

<font size="2"><p style="text-align: center">Tabela 1: FMEA - Autoria Própria.</p></font>

Legenda:

- Ocorrência:
    - 1: Muito improvável
    - 2: Ocorre poucas vezes
    - 3: Ocorre ocasionalmente
    - 4: Ocorre frequentemente
    - 5: Sempre ocorre

- Detecção:
    - 1: Detecção garantida
    - 2: Grande chance de detecção
    - 3: Média chance de detecção
    - 4: Pequena chance de detecção
    - 5: Falha não pode ser detectada

- Severidade:
    - 1: Efeito não detectável no sistema
    - 2: Baixa severidade causando aborrecimento leve
    - 3: Severidade moderada: perda de desempenho perceptível
    - 4: Severidade alta com alta insatisfação
    - 5: Severidade muito alta: risco potencial de segurança e problemas graves de não conformidades

<p style="text-align:justify;">
Ao analisar os resultados, destacam-se os problemas identificados com os maiores Números de Priorização de Risco: a falha de comunicação dos módulos de software e eletrônica, classificada com um risco de 20; seguida pela ausência de um membro devido a questões pessoais ou de saúde, com um risco de 12; e, por fim, os desafios apresentados pelos drivers incompatíveis, também com um risco de 12. Esses achados ressaltam a importância de direcionar esforços para mitigar tais questões, visando garantir o sucesso e a eficiência do projeto.
</p>

## Tabela de versionamento

| Versão| Data | Descrição | Responsável|
|---|---|---|---|
| 1.0 | 13/04/2024 | Criação da tabela de riscos | Diogo Soares, Ciro Costa, Lucas Pantoja  |
| 1.1 | 03/05/2024 | Correção formatação | Artur de Sousa |
| 1.2 | 04/05/2024 | Correção alinhamento e fonte | Ana Carolina |

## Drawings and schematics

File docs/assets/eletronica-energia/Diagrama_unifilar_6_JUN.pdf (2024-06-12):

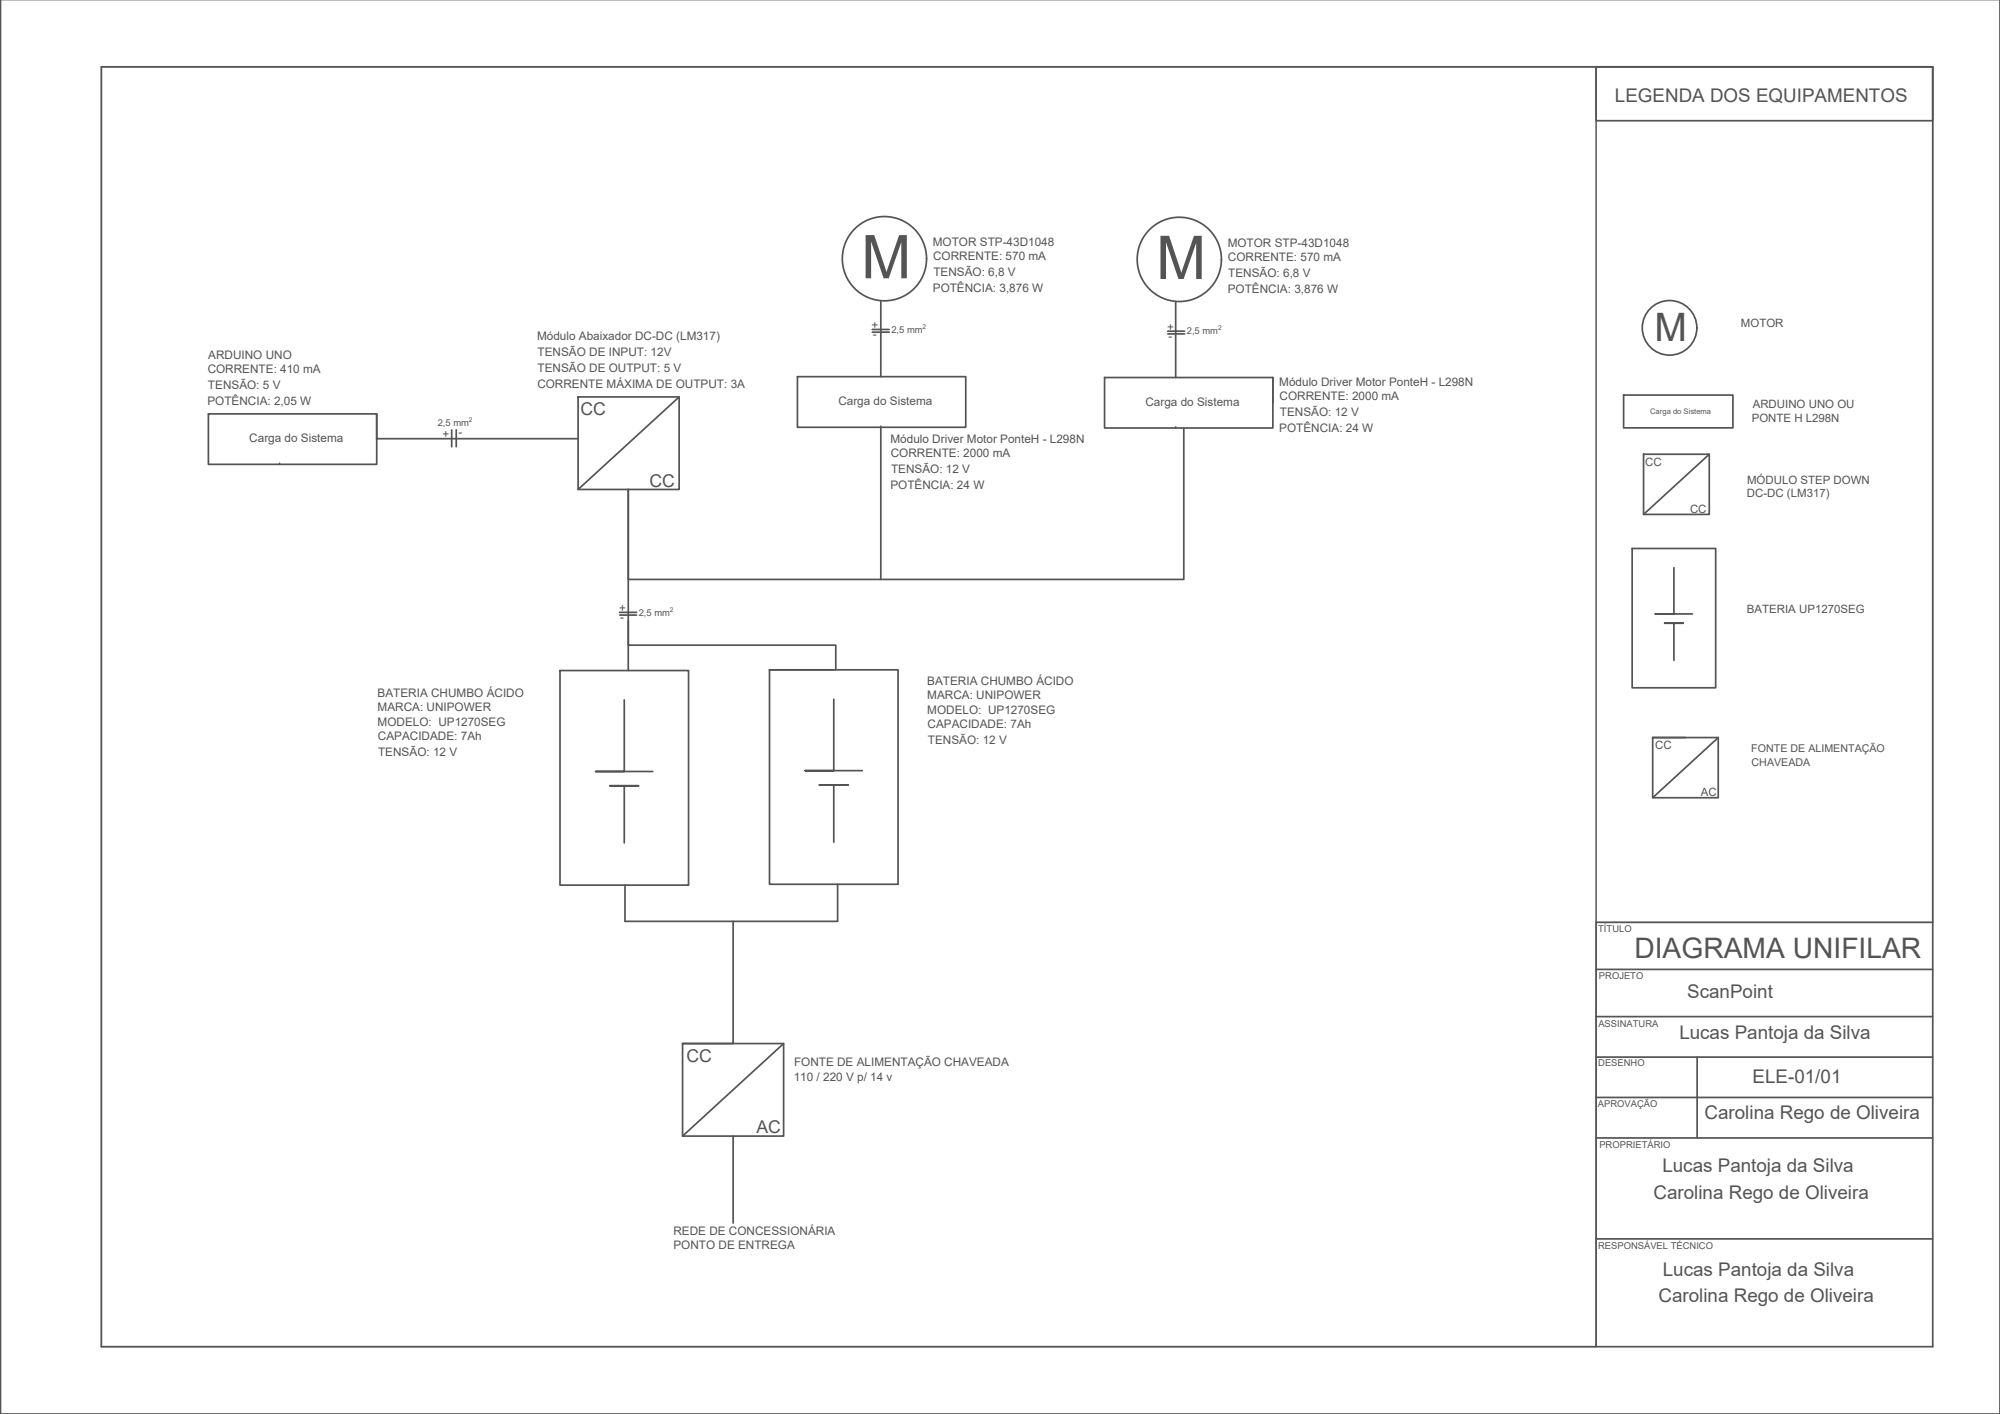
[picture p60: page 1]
M MOTOR STP-43D1048 CORRENTE: 570 mA TENSÃO: 6,8 V POTÊNCIA: 3,876 W BATERIA CHUMBO ÁCIDO MARCA: UNIPOWER MODELO: UP1270SEG CAPACIDADE: 7Ah TENSÃO: 12 V Carga do Sistema ARDUINO UNO CORRENTE: 410 mA TENSÃO: 5 V POTÊNCIA: 2,05 W; Carga do Sistema Módulo Driver Motor PonteH - L298N CORRENTE: 2000 mA TENSÃO: 12 V POTÊNCIA: 24 W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

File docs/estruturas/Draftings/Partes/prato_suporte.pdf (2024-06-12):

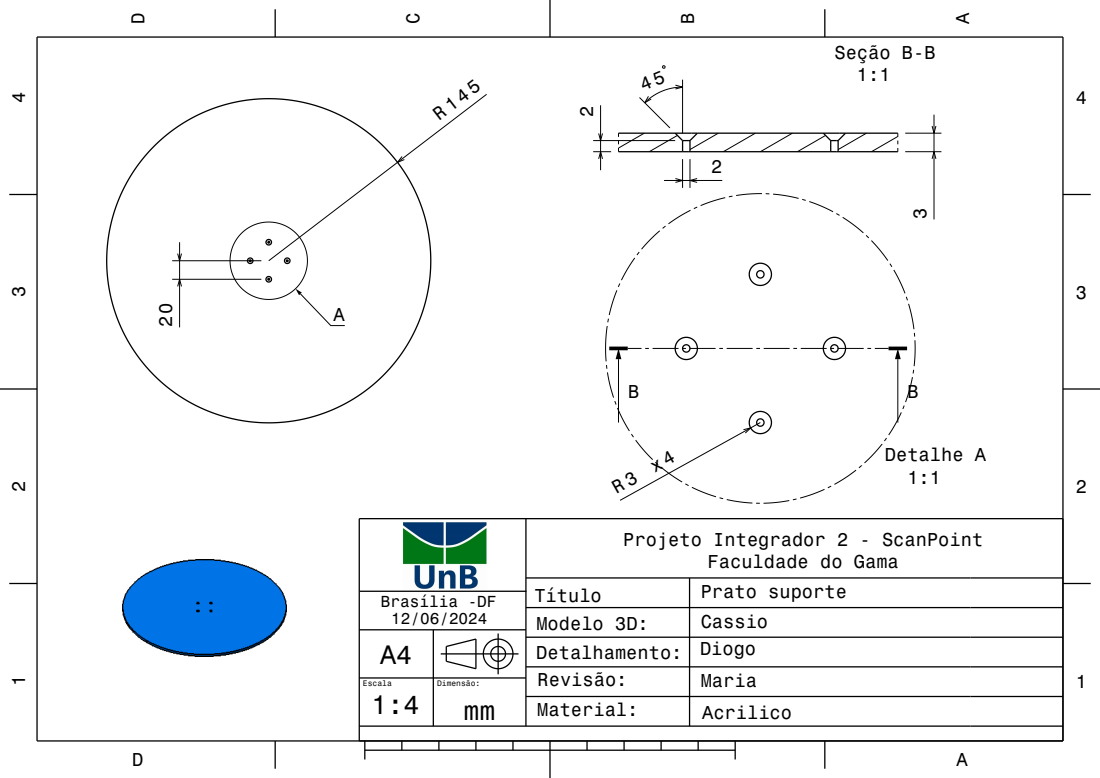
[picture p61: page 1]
Brasília -DF; Título; Detalhe A; Seção B-B

Projeto Integrador 2 - ScanPoint

Faculdade do Gama
Prato suporte

Modelo 3D: | Cassio
Detalhamento: | Diogo
Revisão: | Maria
Material: | Acrilico

A4
1:4 | Dimensão: mm

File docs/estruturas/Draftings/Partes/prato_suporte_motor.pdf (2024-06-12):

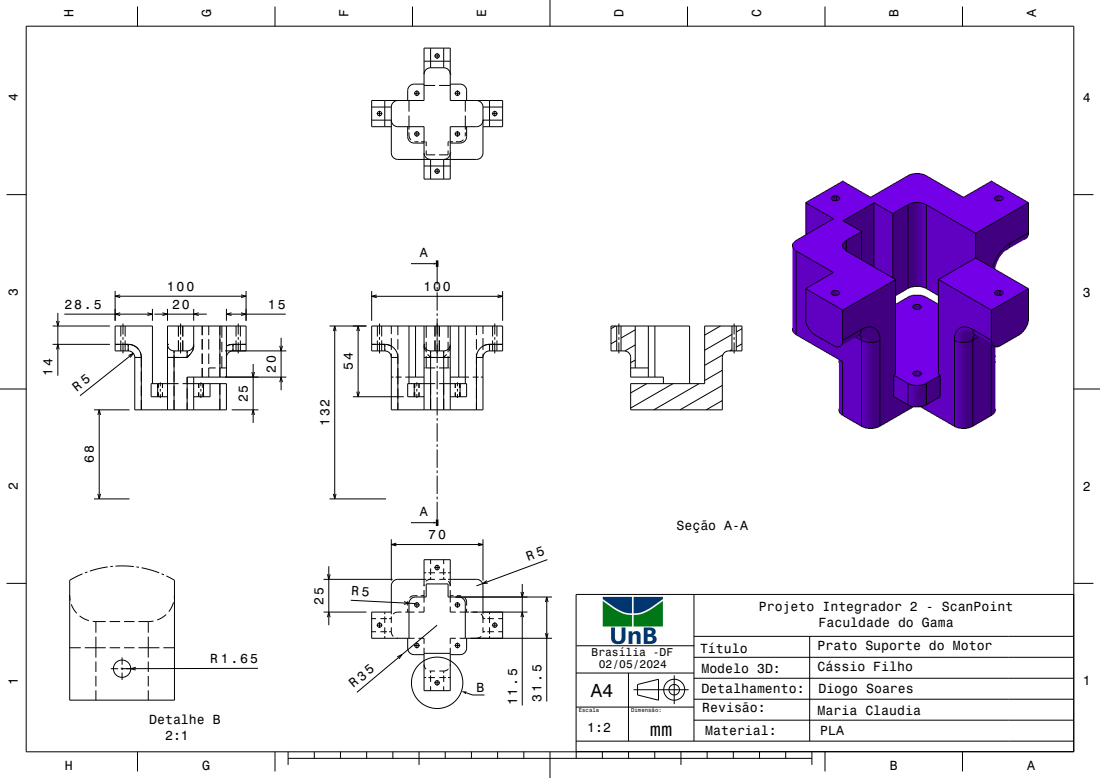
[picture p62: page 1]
Brasília -DF; Seção A-A; Detalhe B

Projeto Integrador 2 - ScanPoint Faculdade do Gama

Título | Prato Suporte do Motor
Modelo 3D: | Cássio Filho
Detalhamento: | Diogo Soares
Revisão: | Maria Claudia

Escala 1:2 | Dimensão: mm
Material: | PLA

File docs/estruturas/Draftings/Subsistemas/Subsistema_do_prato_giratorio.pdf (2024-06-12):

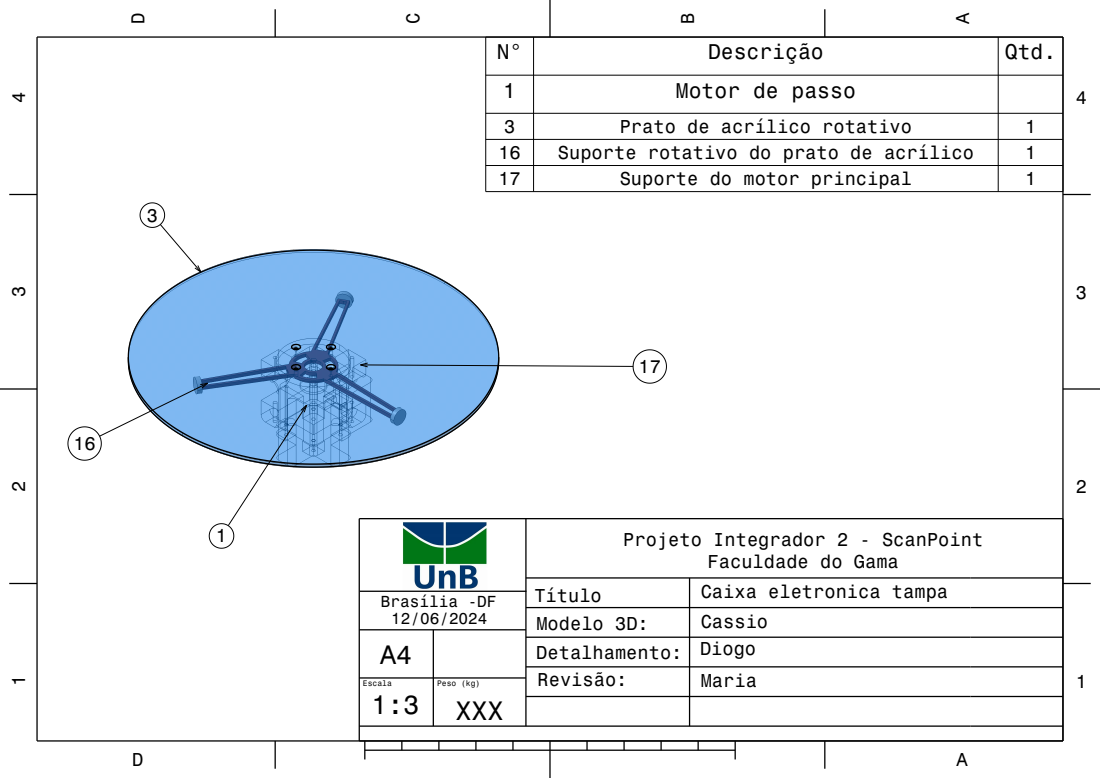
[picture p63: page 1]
Brasília -DF; Título

N° | Descrição | Qtd.
1 | Motor de passo
3 | Prato de acrílico rotativo | 1
16 | Suporte rotativo do prato de acrílico | 1
17 | Suporte do motor principal | 1

Projeto Integrador 2 - ScanPoint

Faculdade do Gama
Caixa eletronica tampa

Modelo 3D: | Cassio
Detalhamento: | Diogo
Revisão: | Maria

A4
1:3 | Peso (kg) XXX

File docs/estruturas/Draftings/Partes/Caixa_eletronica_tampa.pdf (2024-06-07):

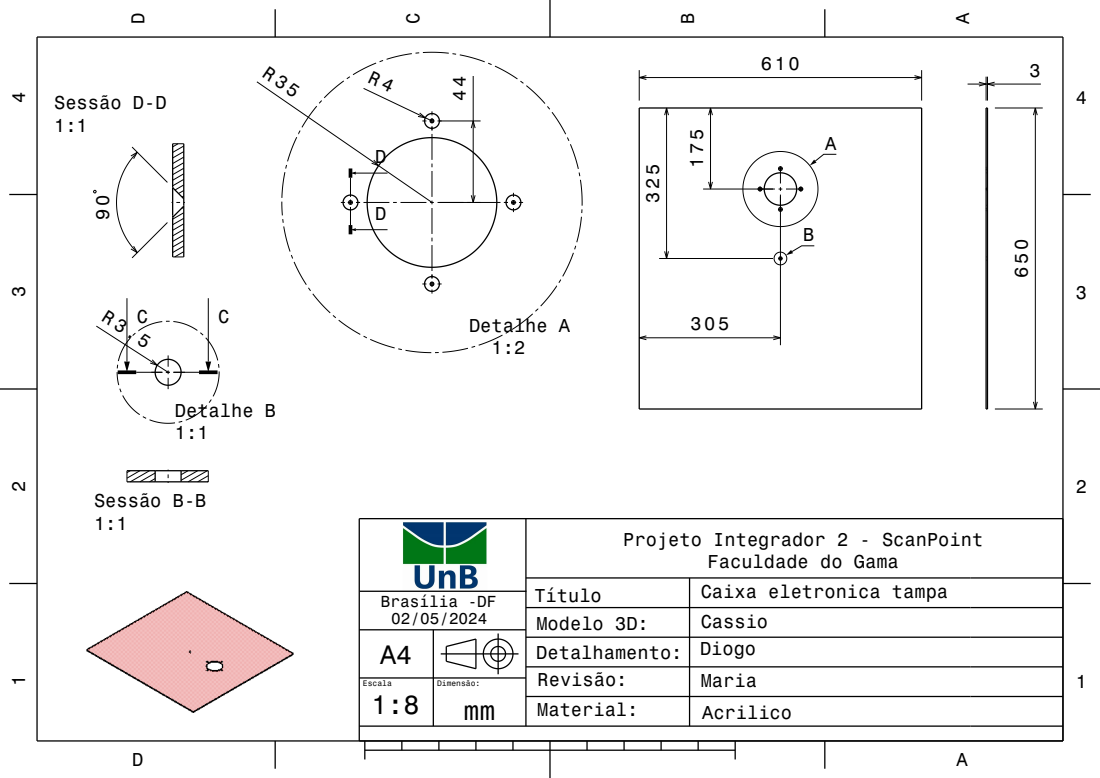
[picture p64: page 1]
Brasília -DF; Detalhe A; Detalhe B; Sessão B-B; Sessão D-D

Projeto Integrador 2 - ScanPoint Faculdade do Gama

Título | Caixa eletronica tampa
Modelo 3D: | Cassio
Detalhamento: | Diogo
Revisão: | Maria
Material: | Acrilico

A4
1:8 | Dimensão: mm

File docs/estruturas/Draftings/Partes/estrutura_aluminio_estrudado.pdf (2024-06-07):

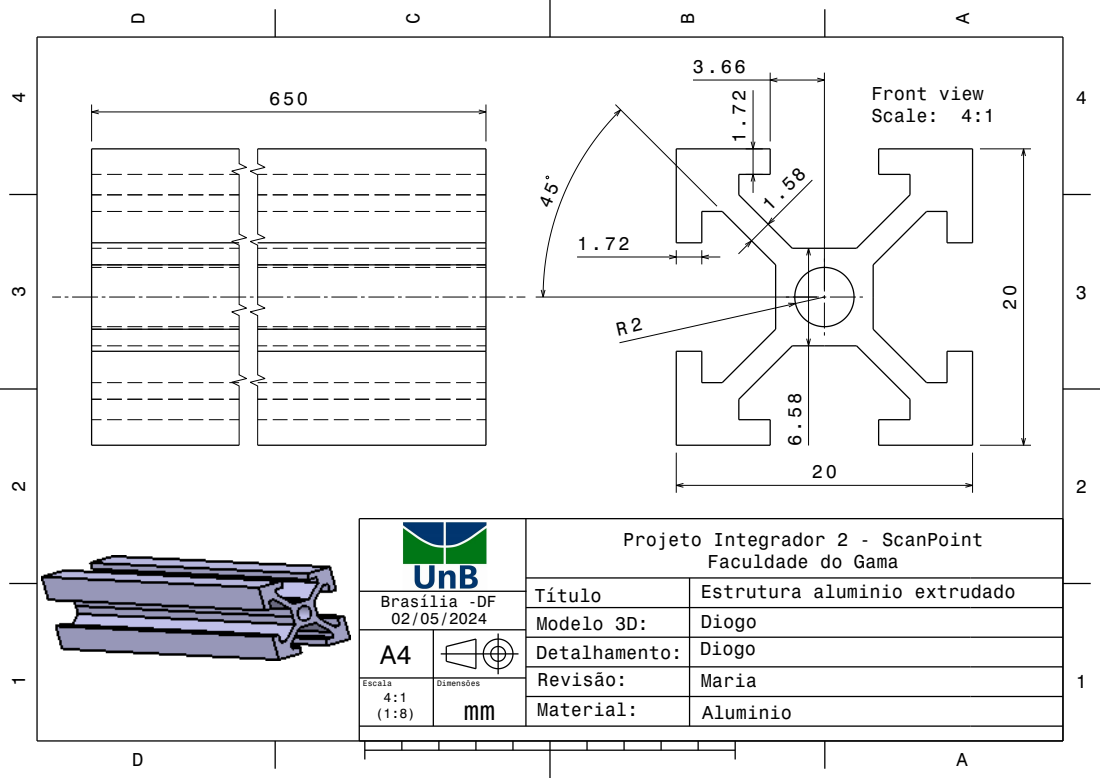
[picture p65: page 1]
Brasília -DF; Front view Scale: 4:1

Projeto Integrador 2 - ScanPoint Faculdade do Gama

Título | Estrutura aluminio extrudado
Modelo 3D: | Diogo
Detalhamento: | Diogo
Revisão: | Maria
Material: | Aluminio

4:1 (1:8) | Dimensões mm

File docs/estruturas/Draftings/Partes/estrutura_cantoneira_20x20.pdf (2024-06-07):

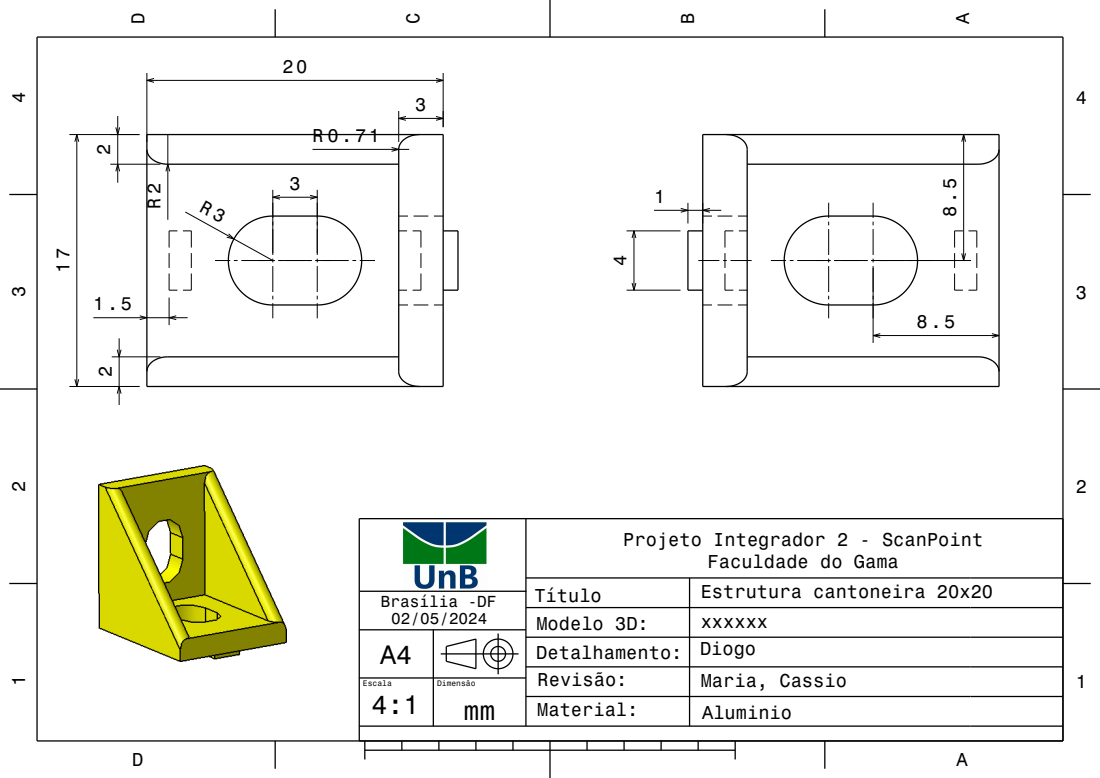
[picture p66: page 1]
Brasília -DF

Projeto Integrador 2 - ScanPoint Faculdade do Gama

Título | Estrutura cantoneira 20x20
Modelo 3D: | xxxxxx
Detalhamento: | Diogo
Revisão: | Maria, Cassio

A4
4:1 | Dimensão mm
Material: | Aluminio

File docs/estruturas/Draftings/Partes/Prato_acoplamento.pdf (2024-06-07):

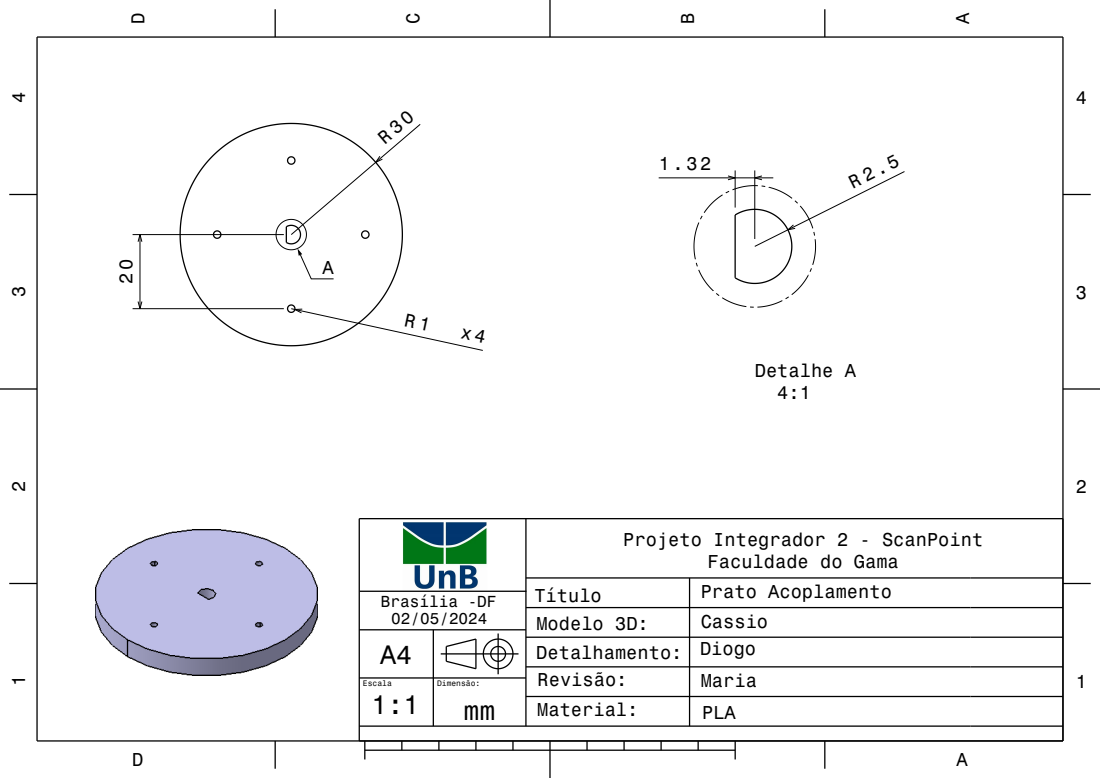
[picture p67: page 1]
Brasília -DF; Detalhe A

Projeto Integrador 2 - ScanPoint Faculdade do Gama

Título | Prato Acoplamento
Modelo 3D: | Cassio
Detalhamento: | Diogo
Revisão: | Maria
Material: | PLA

A4
1:1 | Dimensão: mm

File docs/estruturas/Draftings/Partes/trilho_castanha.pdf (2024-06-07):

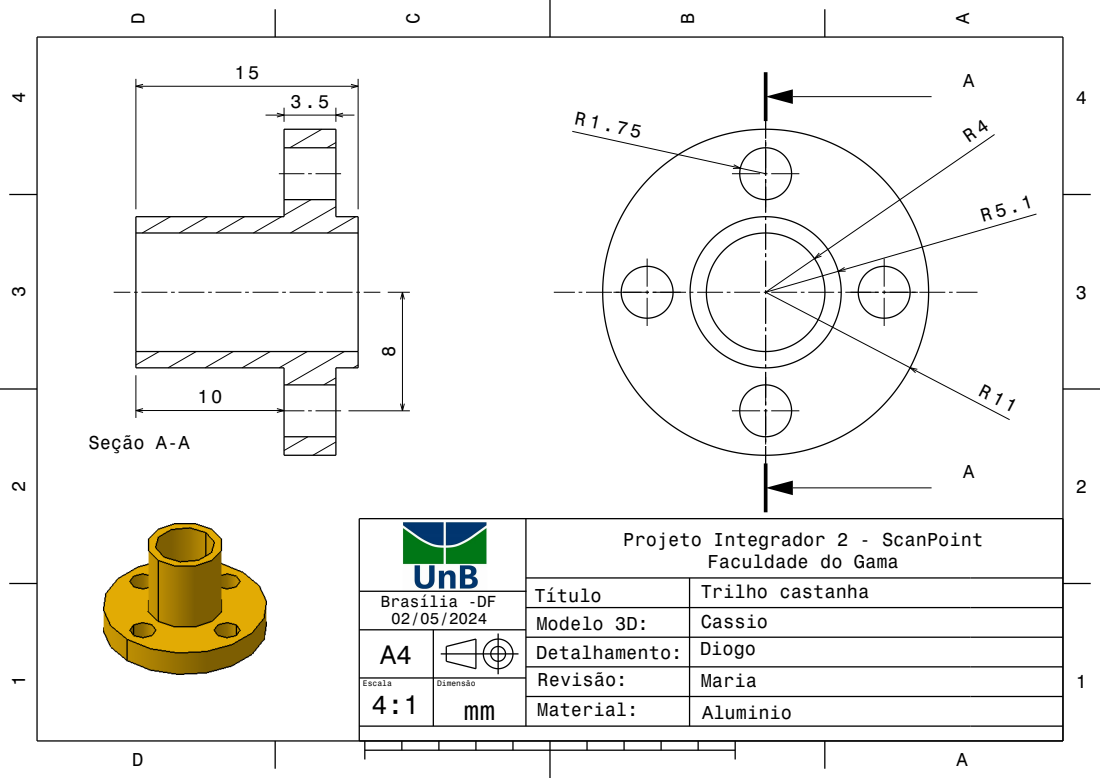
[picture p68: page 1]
Brasília -DF; Seção A-A

Projeto Integrador 2 - ScanPoint Faculdade do Gama

Título | Trilho castanha
Modelo 3D: | Cassio
Detalhamento: | Diogo
Revisão: | Maria
Material: | Aluminio

A4
4:1 | Dimensão mm

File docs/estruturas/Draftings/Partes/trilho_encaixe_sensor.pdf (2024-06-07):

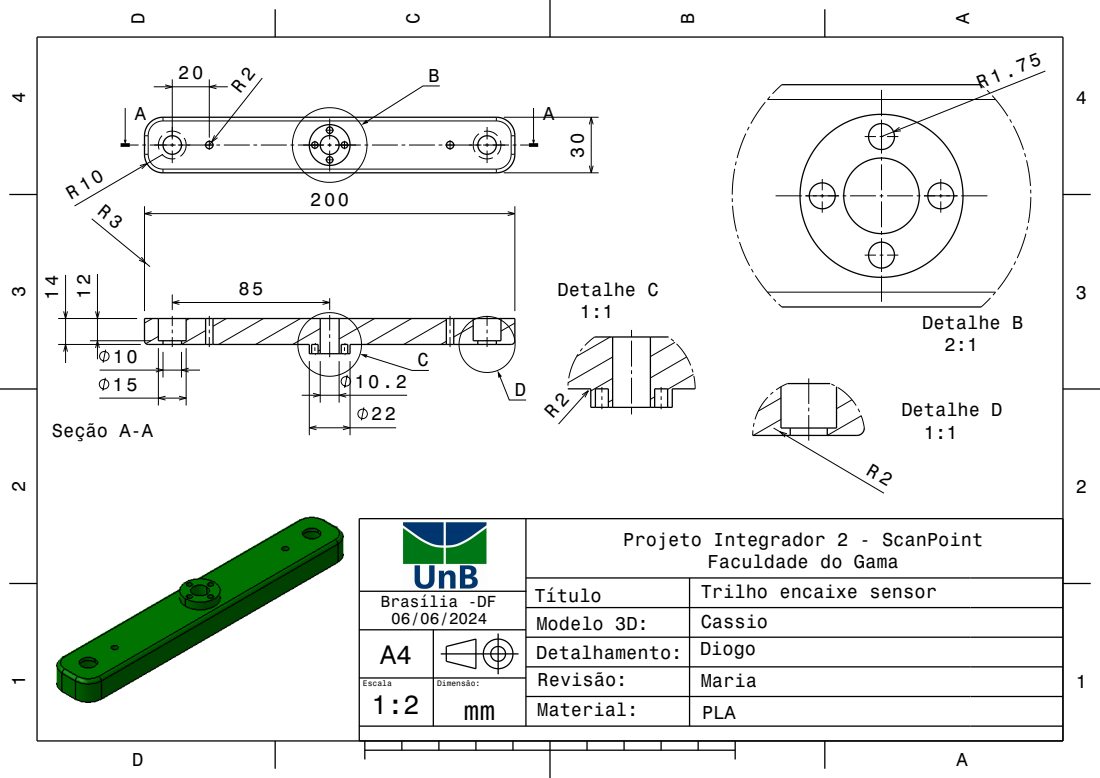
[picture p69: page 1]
Brasília -DF; Seção A-A; Detalhe B; Detalhe C; Detalhe D

Projeto Integrador 2 - ScanPoint Faculdade do Gama

Título | Trilho encaixe sensor
Modelo 3D: | Cassio
Detalhamento: | Diogo
Revisão: | Maria

A4
1:2 | mm

Material: | PLA

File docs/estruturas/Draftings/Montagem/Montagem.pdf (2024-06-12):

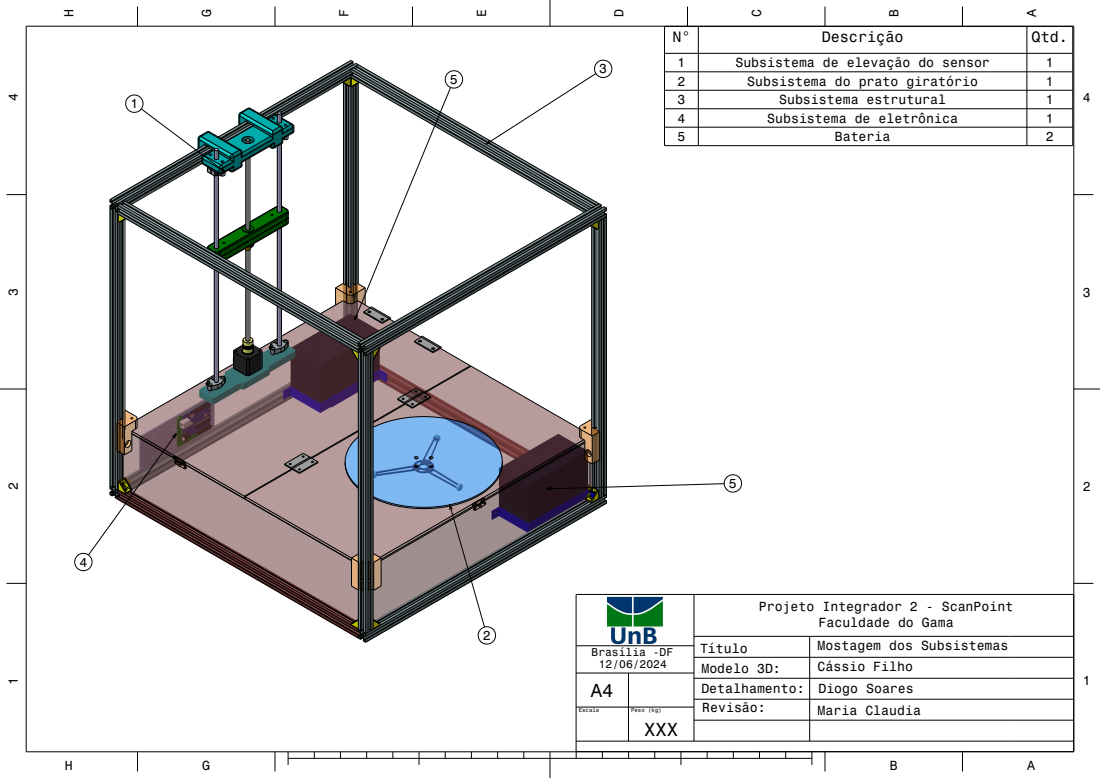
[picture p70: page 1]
Brasília -DF; Título

N° | Descrição | Qtd.
1 | Subsistema de elevação do sensor | 1
2 | Subsistema do prato giratório | 1
3 | Subsistema estrutural | 1
4 | Subsistema de eletrônica | 1
5 | Bateria | 2

Projeto Integrador 2 - ScanPoint

Faculdade do Gama
Mostagem dos Subsistemas

Modelo 3D: | Cássio Filho
Detalhamento: | Diogo Soares
Revisão: | Maria Claudia

Escala | Peso (kg) XXX

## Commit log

2024-04-03 Adicionando ci para o gitlab pages
2024-04-03 Adicionando exemplos e estrutura geral de pastas
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2024-04-12 Adicionado casos de uso ao projeto, modelo inicial
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2024-04-15 Adicionado no read instuções de como rodar os documentos
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2024-04-15 Adicionado Titulo e pequeno ajuste na introdução do levantamento de riscos do FMEA
2024-04-17 Retirado frete do preço de partes eletrônicas internacionais
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2024-04-19 excluindo arquivo de teste e adicionando arquivos de CAD na pasta CAD em estruturas
    [Bateria.CATPart, Caixa_Eletronica.CATProduct, Caixa_eletronica.CATPart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]
2024-04-20 Criação do diagrama de protocolo de comunicação de software
2024-04-23 fix[documento de visao]: Melhoria da introdução, inclusão da soluções de mercado e alterção da posição do produto
2024-04-23 Preenchimento dos tópicos 8.3 ao 8.5, ajustes na formatação e na instrução de posição do produto
2024-04-23 componentes e suportes addicionados a montagem
    [A4988.CATProduct, A4988.stl, A4988.stp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]
2024-04-24 atualização do diagrama de software e redigido texto de explicação dos componentes
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2024-04-25 modificações no CAD
    [A4988.CATProduct, A4988.stl, A4988.stp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]
2024-04-25 organização das pastas do CAD
    [Bateria.CATPart, Iluminacao.CATPart, Prato.CATPart]
2024-04-25 Imagens utilizadas no relatório em assuntos voltados a estrutura do projeto.
2024-04-25 Upload do diagrama do EAP de estruturas em imagens
2024-04-25 Update do link do EAP de estruturas em index.md
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2024-04-28 docs: atualiza diagrama e documento de casos de uso
2024-04-28 modificado diagrama e concluído o documento de arquitetura
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2024-04-29 Gh pages
    [A4988.CATProduct, A4988.stl, A4988.stp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]
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2024-04-29 Edição de texto, tabelas e uma possível imagem
2024-04-29 adicionado arquivo de subsistema de software e processamento pointcloud
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2024-04-29 Adicionado o documento de requisitos no mapeamento de páginas do MkDocs
2024-04-29 Adição de alguns requisitos funcionais e não funcionais, e também a formatação do documento para melhor visualização em tabela, colocando um código (id) para cada um dos requisitos listados
2024-04-29 Diagrama Unifilar • Arquivo DWG
    [Diagrama_unifilar.dwg]
2024-04-29 Criação do documento de descrição do diagrama de BPMN, assim como a devida vinculação do diagrama para visualização, adicionado também a indexação do mkdocs.yml o acesso ao documento pelo nome de
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2024-04-29 Adicionado documento de funcionalidades do projeto, juntamente com a tabela com suas devidas histórias de usuário e priorizações seguindo o método MoSCow
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2024-04-30 Ajustes gerais no doc
    [Diagrama_unifilar.dwg]
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2024-05-02 deletando pasta estruturas raiz e adicionando CAD suporte na pasta de estruturas
    [A4988.CATProduct, A4988.stl, A4988.stp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]
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2024-05-02 Adicionando texto de termo de abertura do projeto
2024-05-02 Update link para o termo de abertura do projeto index.md
2024-05-02 Update link para o termo de abertura do projeto README.md
2024-05-02 Atualização da lista de artefatos entregas no PC1
2024-05-02 Atualização dos caminhos para os arquivos que compõe o relatório 1
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2024-05-02 Atualizando os links do EAP de Estrutura e de Eletrônica-Energia
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2024-05-02 Acrescentando o link das normas e dos requisitos de Eletrônica e Energia
2024-05-02 Ajuste dos caminhos para o formato que a Brenda fez
2024-05-02 adicionando folha de fundo na pasta Draftings e modificando peça de suporte do motor
    [Caixa_eletronica.CATPart, suporte do motor.CATPart]
2024-05-03 doc: refatoração de nomes, ajustes na introdução, inclusão de soluções comerciais e alteração da instrução de posicionamento do produto
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2024-05-03 adiconando draftings de subsistemas e ordenando as plantas em pastas
    [Caixa_eletronica.CATPart, Estrutura.CATProduct, Scanner.CATProduct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]
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2024-05-03 atualização drawings
    [Bateria.CATPart, Caixa_eletronica.CATPart, Estrutura.CATProduct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]
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2024-05-03 Ajuste efetuado em casos de uso e diagrama bpmn
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2024-05-04 Criando classe zoom para dar zoom nas imagens
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2024-05-04 doc: atualizacao do titulo e erros de portugues
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2024-05-16 coirreção dos desenhos técnicos
    [aluminio_estrutural.CATPart]
2024-05-20 Criação de documento de público-alvo e de personas
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2024-06-06 mudança no CAD do trilho do sensor
    [ANSI_B_18_3_1M_M5x25_STEEL_HEXAGON_SOCKET_HEAD_CAP_SCREW.CATPart, Encaixe_Trilho.CATPart, Encaixe_Trilho_Inferior.CATPart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]
2024-06-07 modificações no cad do trilho
    [Caixa_Eletronica.CATProduct, Encaixe_Trilho.CATPart, Encaixe_Trilho_Inferior.CATPart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]
2024-06-07 Update modificação de imagens "Barramento" e "Diagrama Unifilar" Projeto_Subsistema_Energia.md
2024-06-07 atualização dos DTs
    [A4988.CATProduct, Caixa_Eletronica.CATProduct, Estrutura.CATProduct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]
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2024-06-07 atualização sem eletrônica
    [Base.CATPart, Caixa_Eletronica.CATProduct, Caixa_eletronica.CATPart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]
2024-06-07 atualização do CAD para entrega
    [Caixa_montada.CATProduct, Estrutura.CATProduct, Lateral_Maior.CATPart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]
2024-06-12 Atualização do link embutido do diagrama de pacotes
2024-06-12 Atualização para entrega de estruturas
    [A4988_1.CATPart, Array003.CATPart, Array004.CATPart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]
